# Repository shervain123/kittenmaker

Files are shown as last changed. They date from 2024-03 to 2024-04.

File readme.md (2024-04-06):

# kittenmaker

*kittenmaker* - an ESP32 based msla 3d printer

*originally created by [NyaCat42](https://github.com/NyanCat42/kittenmaker)*

# Work in progress
Parts list and instruction may be inaccurate and will be change

~As of currently I'm still waiting for all the parts to arrive~

~Parts have arrived and just notice some problems<br> fortunately it's just wrong size of magnet which I have reorder~

Wiring and pins are based off of online resources and codes

## Features 

- Web interface
- g-code parsing
- mid-print parameter updating
- magnetic, easily removable vat and printbed

## Hardware

 1. 3D printed parts in the [3D models folder](https://github.com/shervain123/kittenmaker/tree/main/3d%20models)
 2.  A Bic Crystal pen or something similar (I used a pencil)
 3. T5 lead screw and nut (the nut needs to be in a rectangle shaped instead of circular shaped)
 4. M2 & M3 screws
 5. 3w UV led 405nm wavelength
 6. A 5v fan with heat sink
 7. FEP film
 8. Bearings (683ZZ or 3x7x3mm) x6
 9. Esp32 S2 mini
 10. 2.4inch tft SPI ILI9341 display (no touch and no adapter board)
 11. Parts for driving the led (can be modified with whatever parts you have like relay)
	 -	IRFZ44N mosfet
	 -	2.2 Ohm 5W resistor
12. ~4x3mm~ 5x2mm magnets x16
13. 28byj-48-5v stepper motor with uln2003 driver
14. Micro switch
15. SD Card reader (NOT DFPlayer)

## 3D models
it is recommended to print with PETG as it is much more UV resistance than PLA but you could try and use UV protective coating on the  parts that are more likely exposed to the UV light

 ~~You will also need to print the legs.3mf and post.3mf 4 times~~ Designed a new feet / fan cover.
 
 Also for some odd reason the original does not include any way to connect the motor to the lead screw but I did find a model in older version of it which I included in the 3D models folder 

Bottom was redesigned to move the SD card and Wemos to a different location to free up some space and included screw points for the bottom feet.

## Instructions
I have decided to split them out you can find them [here](https://github.com/shervain123/kittenmaker/blob/main/instruction.md)

## Known Issue / WIP issue
Faced an issue where ESP32S2 failed to initialized and bootlooping. ~~Issue was caused by a cheap unbranded SD card that does not support SPI~~ (The SD card worked at a later date)(seems like wiring issue on the sd reader) 

Used paint primer to smooth out the resin tray, turns out primer is not resin safe. oops.

Magnet protruding from the bottom of the resin tray caused the FEP film to not seal properly and caused leaks. Might need to edit the model depending on how well your printer prints.

FEP film does NOT stick to any adhesive (tried super glue, hot glue, liquid nail(?) ), only solution that worked is sticking it with double sided tape and sealing around the tray with packing tape. 

Aluminum tape on build plate has a lot of creases, and apparently the adhesive melts in resin. Replaced with flatten soda can cut to size and superglued onto the build plate.

Z axis wobbles left to right while raising / lowering the build plate, not currently fixed and is still a work in progress. 

Benchy was printed as [Bchy](https://github.com/shervain123/kittenmaker/blob/main/images/bchy.jpg) :D

## Software

Slicer [Chitubox](https://www.chitubox.com/en/download/chitubox-free)<br>
[Chitubox v1.8.1](https://sac.chitubox.com/software/download.do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)
(Honestly I don't really like it but I don't know any better alternative so I'm stuck with this one)
<br>also if you are using newer version you will need software like uvtools to convert the ctb file to a zip. Older version can save as zip files

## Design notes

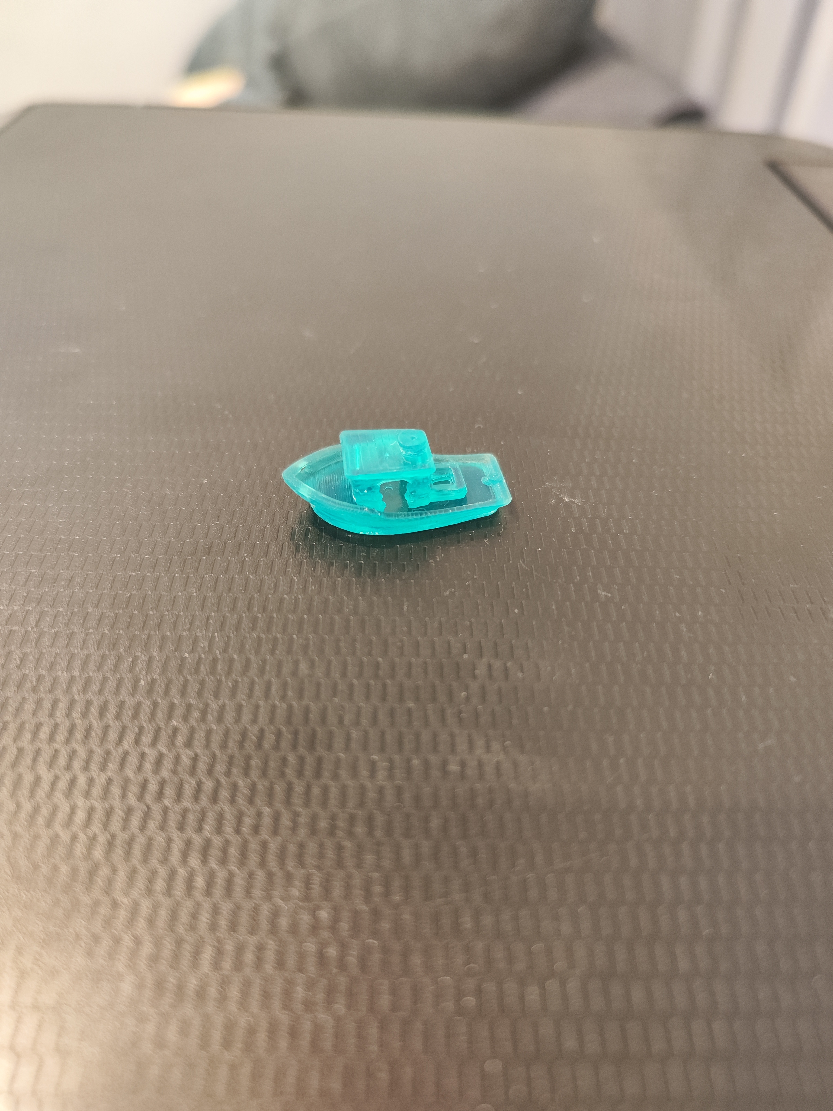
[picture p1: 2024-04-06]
images/bchy.jpg

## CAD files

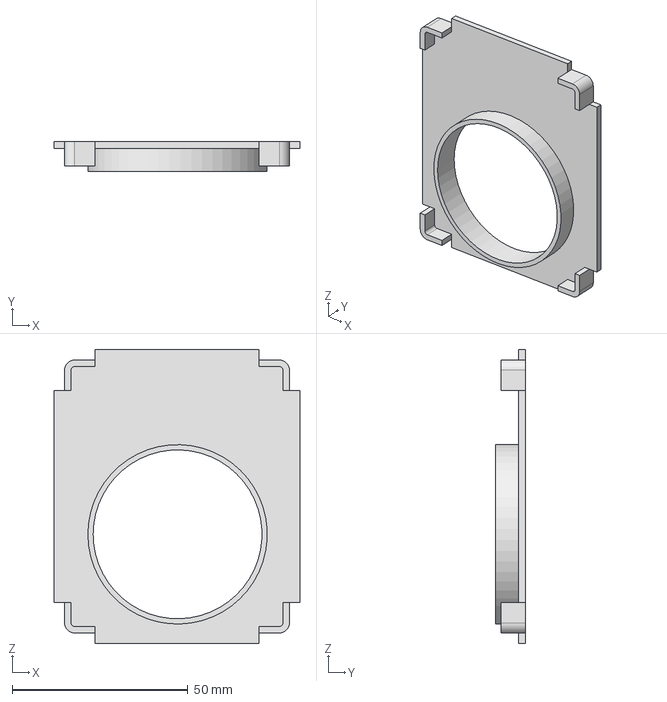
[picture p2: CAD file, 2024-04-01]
3d models/bottom cover.stp
69.9 x 8.50 x 83.6 mm

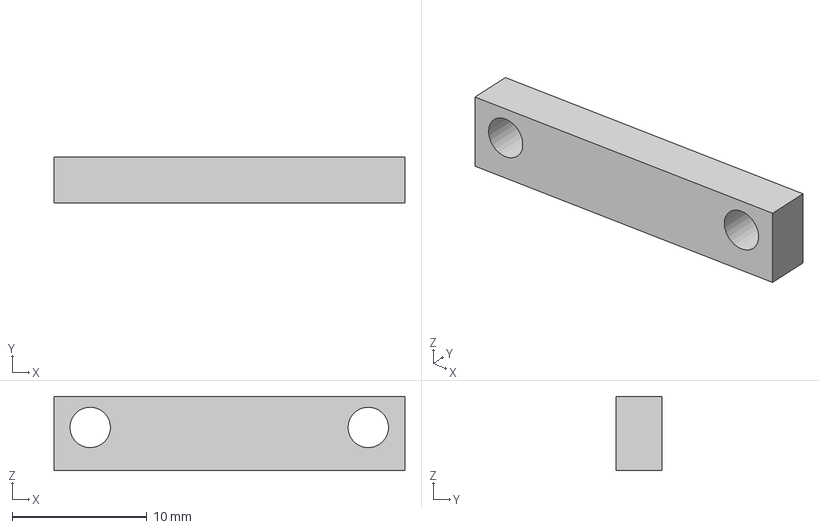
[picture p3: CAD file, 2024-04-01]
3d models/spacer.3mf
26.0 x 3.40 x 5.50 mm

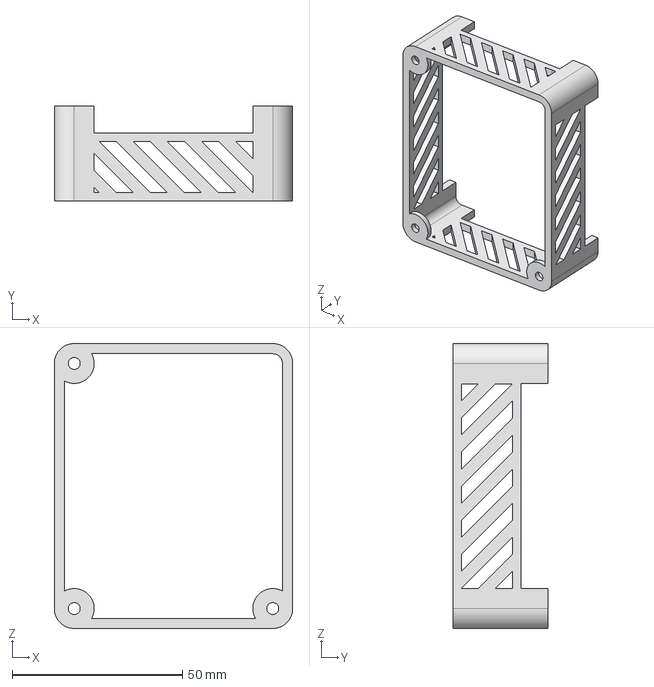
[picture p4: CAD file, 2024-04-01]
3d models/bottom.stp
69.9 x 28.0 x 83.6 mm

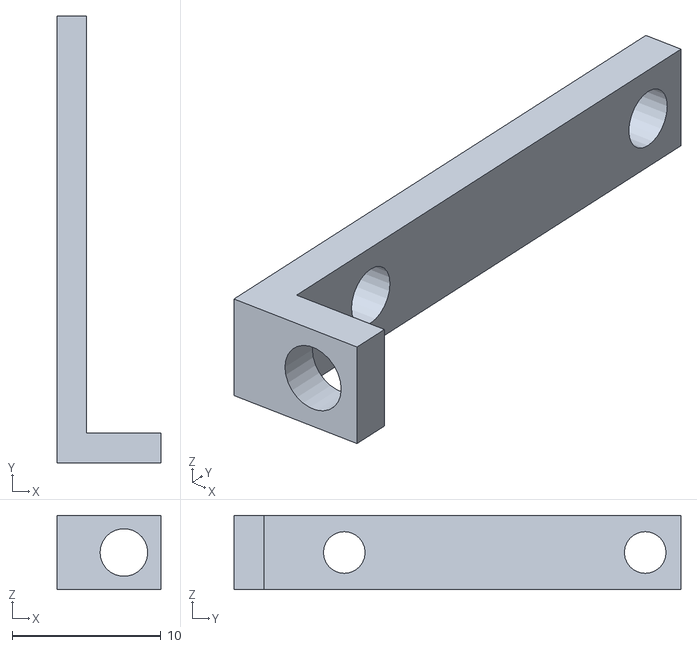
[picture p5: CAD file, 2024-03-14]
3d models/board holder.stl
7.00 x 30.0 x 5.00

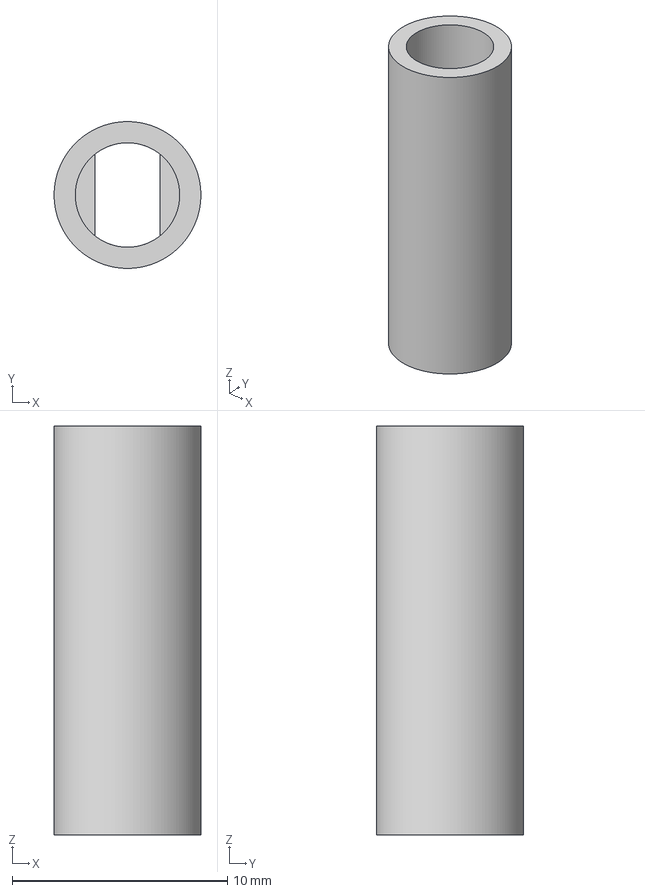
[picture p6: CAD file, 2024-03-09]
3d models/coupler.3mf
6.82 x 6.82 x 19.0 mm

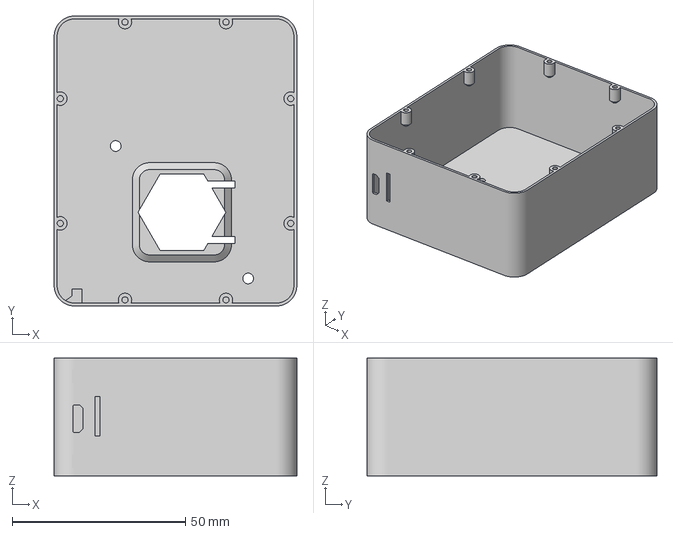
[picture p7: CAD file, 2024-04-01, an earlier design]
3d models/old/bottom (1).3mf
69.9 x 83.6 x 34.0 mm

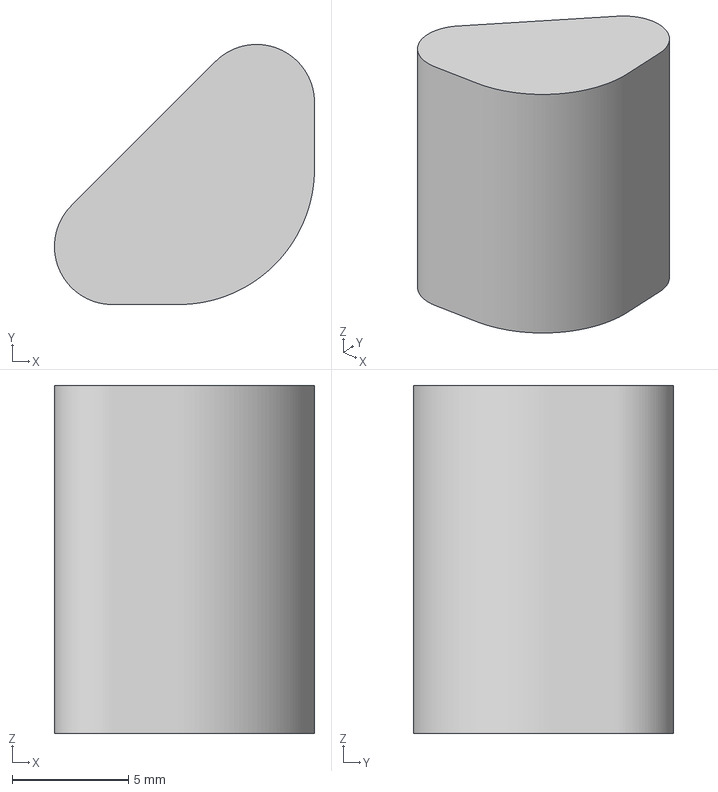
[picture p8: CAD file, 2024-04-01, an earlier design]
3d models/old/leg.3mf
11.2 x 11.2 x 15.0 mm

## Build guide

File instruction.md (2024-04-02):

[here](https://github.com)

## Wiring

### !!! WARNING ALWAYS DOUBLE CHECK WIRING BEFORE PLUGGING IN POWER AND MAKE SURE TO TEST IT BEFORE SOLDERING INTO THE BOARDS AND DISPLAY

### THE DISPLAY WIRE IS VERY CLOSE TO EACH OTHER PAY ATTENTION DURING SOLDERING AND CHECK WITH MULTIMETER THERE IS NO SHORT

The wiring is based on the code and my testing

| Item | ESP32 |
| --- | --- |
| UV LED | GPIO 37 |
| Home switch `<br>`(low trigger) | GPIO 39 |
| **Stepper motor** | |
| Pin 1 | GPIO 35 |
| Pin 2 | GPIO 33 |
| Pin 3 | GPIO 18 |
| Pin 4 | GPIO 16 |
| **SD CARD** | |
| CS | GPIO 1  |
| MOSI | GPIO 11 |
| CLK | GPIO 7  |
| MISO | GPIO 9  |
| 3v3 | 3v3 |
| **TFT DISPLAY** | |
| MISO(SDO) | GPIO 9  |
| MOSI(SDI) | GPIO 11 |
| SCLK(SCL) | GPIO 7  |
| CS(CSX) | GPIO 12 |
| DC | GPIO 5  |
| RST | GPIO3 |

If there is any problem feel free to let me know

This is the pinout for my display please check with your display first
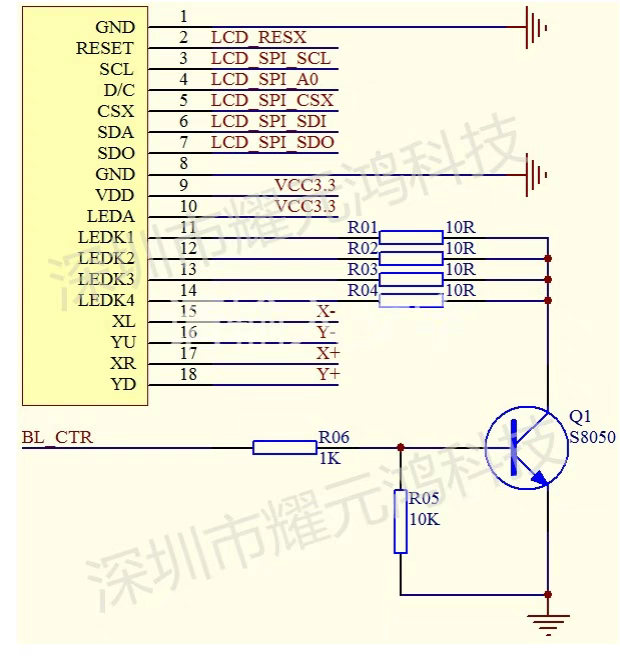
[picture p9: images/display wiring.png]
wirings


## Building instructions

This instructions is for the new bottom which I have modified from the original and with the help of tormenmashi_

If you want to follow with the original instruction, it can be found [here](https://github.com/shervain123/kittenmaker/blob/main/instruction%20old.md).

tbh this is all over the place so you should just use this as a guide for what parts goes where (I have no idea what im doing)

1. ~~Cut a piece of aluminum tape and stick it on the build plate~~ Turns out aluminum tape is trash instead, cut a aluminum can and stick it on using super glue
2. Use aluminum tape to cover the inside light tunnel to help the light disperse better
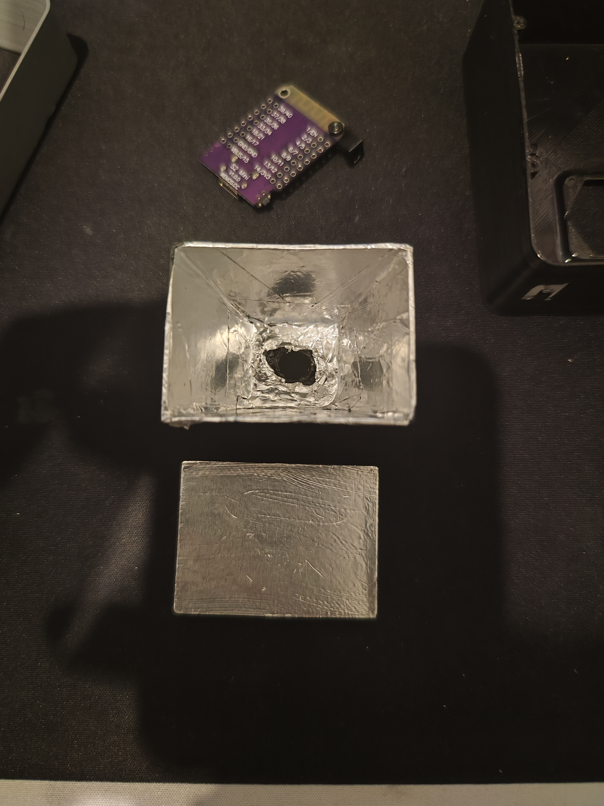
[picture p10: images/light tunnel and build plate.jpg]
Both build plate and light tunnel
   
3. Screw the bottom to the bottom case using 3 M3 screw and nuts
4. Solder wires to the sdcard board and screw it into the bottom case using 2 M2 screw and nuts
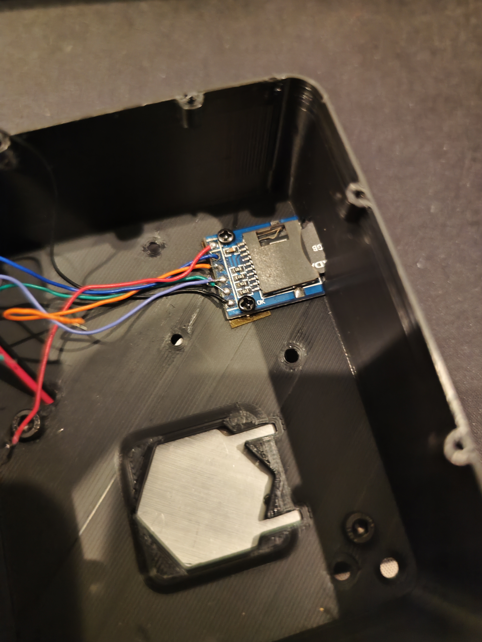
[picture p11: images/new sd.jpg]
SD screw in
   
5. Screw the wemos s2 mini with the spacer
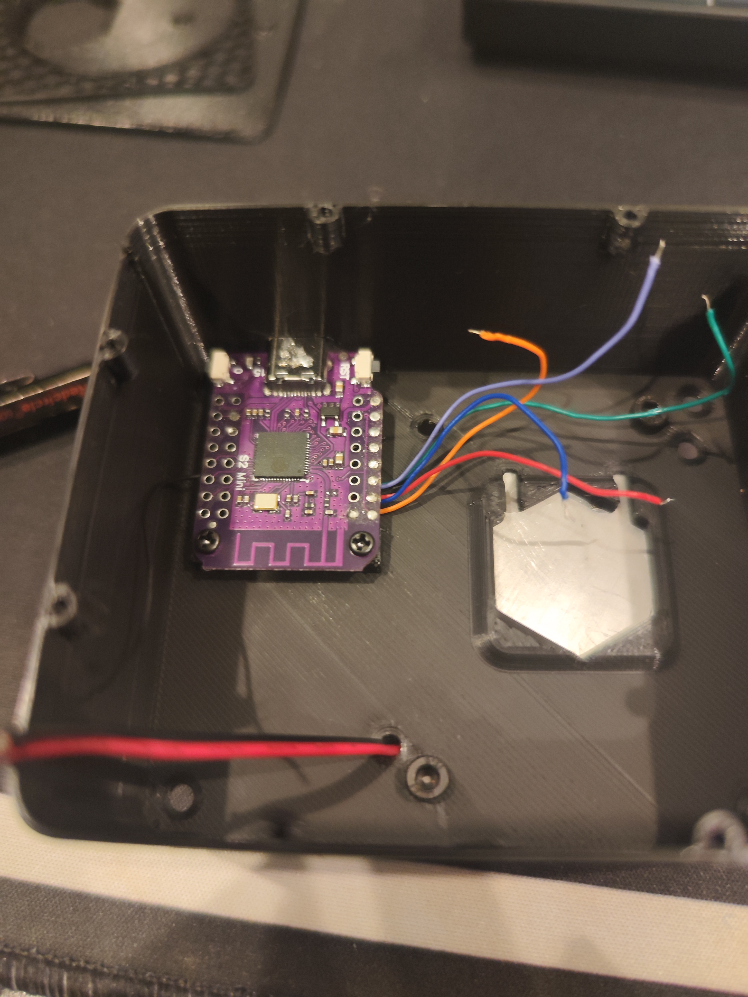
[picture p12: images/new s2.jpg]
wemos screw in
   
6. Next screw in your fan and pass the wire through the hole
7. Remove the lcd from the frame, the metal backing can be removed using a flat head screwdriver then gently bend the plastic part backwards to loosen the glue and slow the display will pop out
8. make sure you remove all the backlight component from the display and you should be left with a lcd that is see through dimly
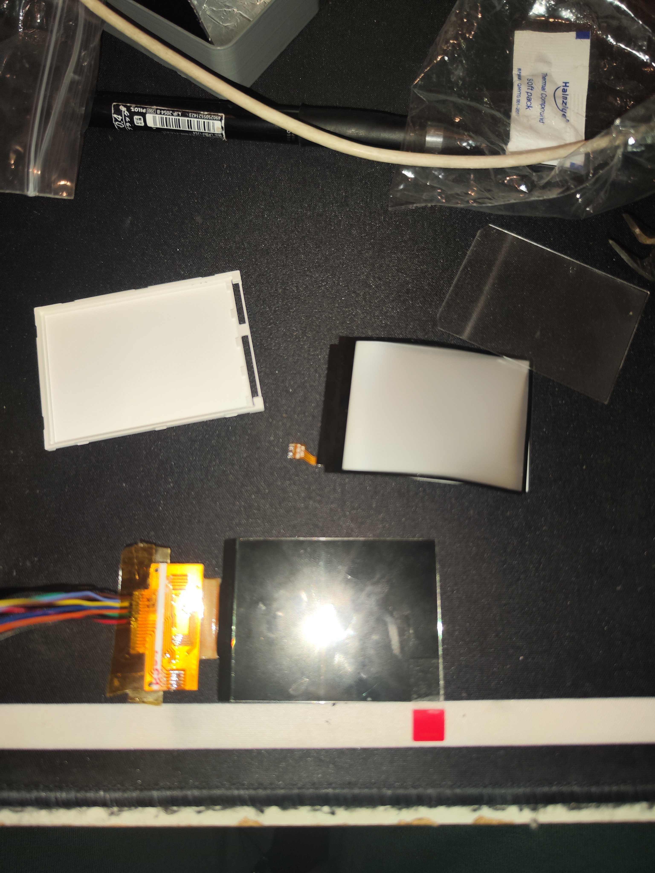
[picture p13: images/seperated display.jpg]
Naked display
   
9. pass all the wires and ribbon into the hold on the top case and place the display in it's place DO NOT FORCE IT IN IF IT DOESN'T FIT take it out and cut the edges of the top half NOT THE DISPLAY
10. Screw in the motor and the micro switch as well (use m2x10 for the switch)
11. Your finished top half should look something like this
    Top half
12. Then finished the bottom half by soldering the leds, motor controller and fan
13. Then you should solder both the lcd and sd card wires (based on the wiring diagram
14. After checking your connection plug it in  and test is everything worked
15. Screw the board to the bottom case and glue the sd card to the back
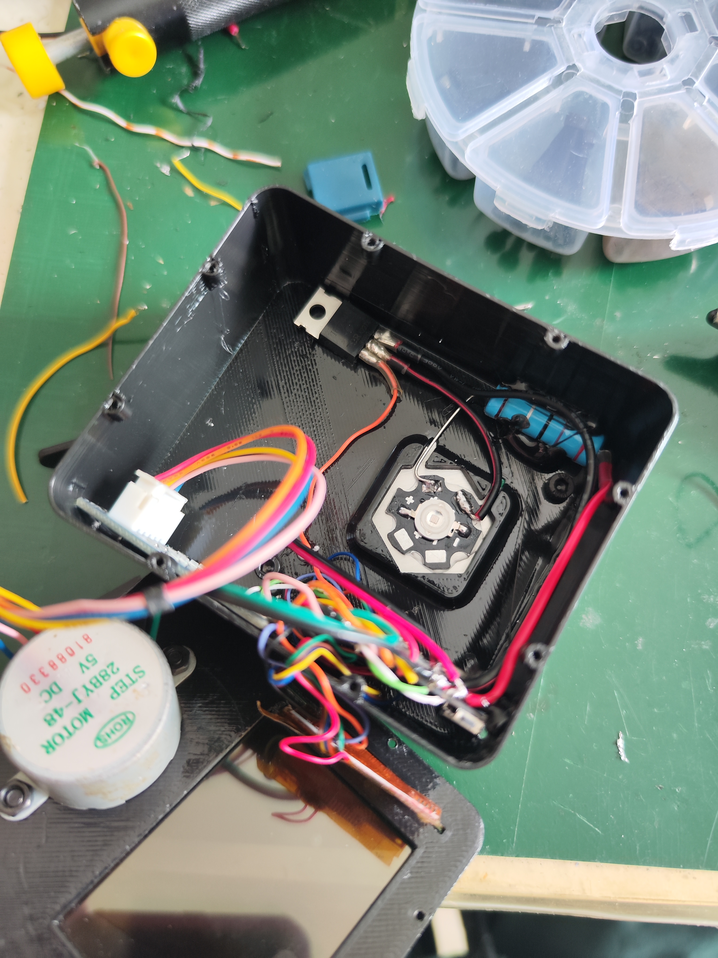
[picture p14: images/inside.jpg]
inside
    
16. Then screw in the top case with m2x4 screw
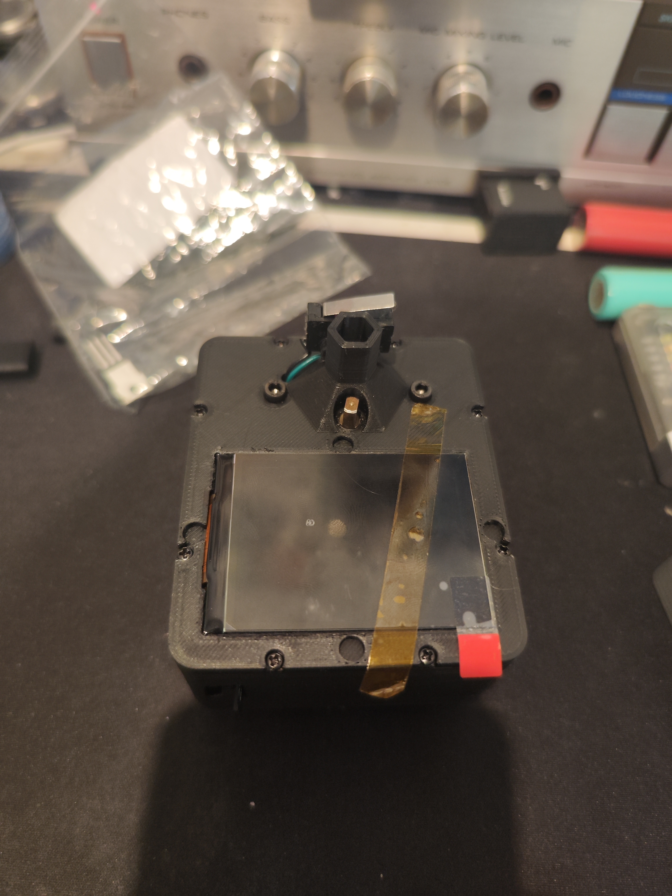
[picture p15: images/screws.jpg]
completed bottom part
    
17. Glue the feet to the bottom of the case and put coupler onto the motor
18. add glue to your bic pen and shove it in the hexagon shaped hole on the bottom and insert your lead screw into the coupler
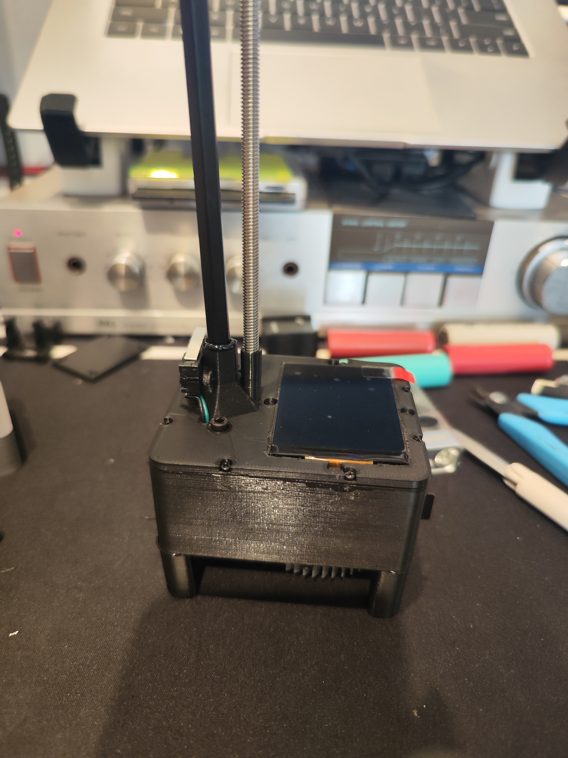
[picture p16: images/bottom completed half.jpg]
pencile
    
19. Take the top part and insert your lead screw nut you will need to drill the hole for it
    top part
20. Put the 6 bearing in place and use M3 screw to secure it in place (I run out of shorter screw)
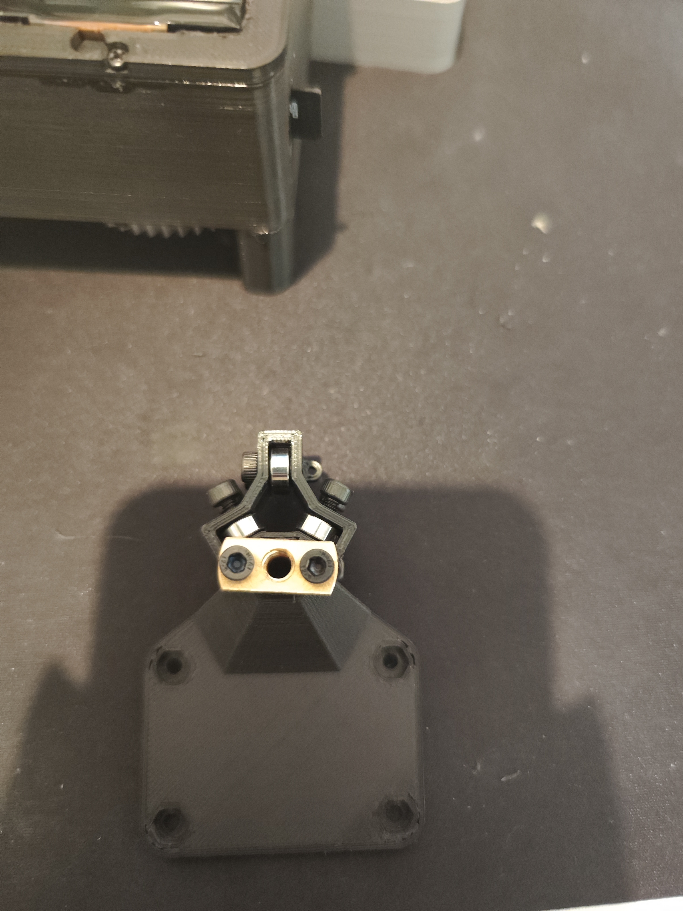
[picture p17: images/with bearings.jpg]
now with bearings!
    
21. Place 4 M3 nut in place and find the longest M3 screw you have to screw it in
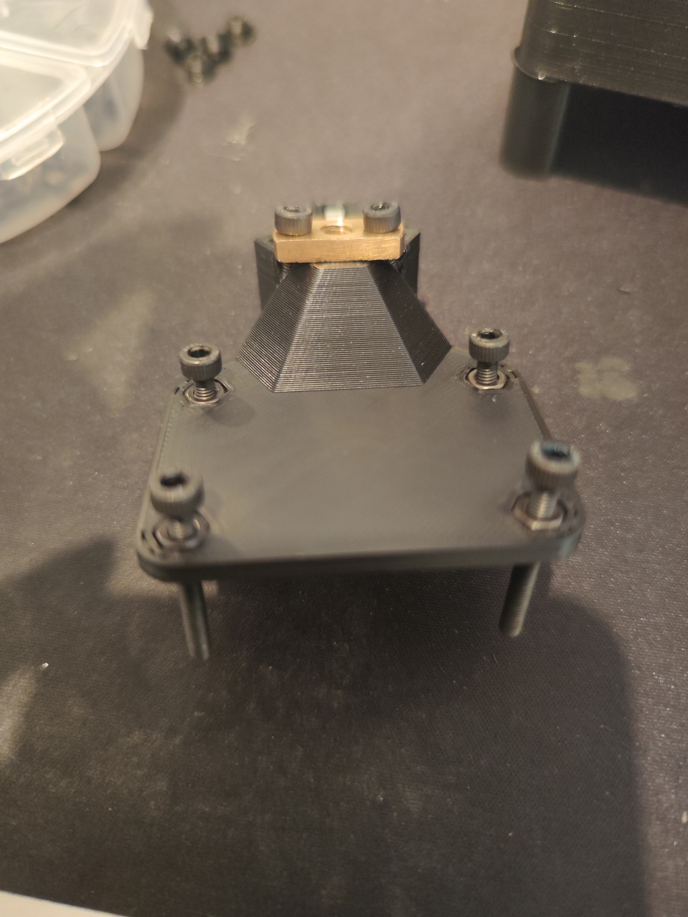
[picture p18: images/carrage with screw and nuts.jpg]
now with nuts!
    
22. Screw the plastic peg into the screw
    Pegs
23. add the longest m2 screw you have to the small part at the bearing side (this function as a home switch adjuster thingy)
24. place the magnet in all the places needs it (vat,case top, build plate and the just fron just now)
25. stick the FEP film on the vat with double side tape 
26. I have no idea how to attach the fep film superglue doesn't work
27. i think that's about it

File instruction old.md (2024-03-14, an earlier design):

## Wiring
### !!! WARNING ALWAYS DOUBLE CHECK WIRING BEFORE PLUGGING IN POWER AND MAKE SURE TO TEST IT BEFORE SOLDERING INTO THE BOARDS AND DISPLAY

### THE DISPLAY WIRE IS VERY CLOSE TO EACH OTHER PAY ATTENTION DURING SOLDERING AND CHECK WITH MULTIMETER THERE IS NO SHORT

The wiring is based on the code and my testing

|Item|ESP32  |
|--|--|
|UV LED| GPIO 37 |
|Home switch <br>(low trigger)|GPIO 39|
|**Stepper motor**||
|Pin 1|GPIO 35|
|Pin 2|GPIO 33|
|Pin 3|GPIO 18|
|Pin 4|GPIO 16|
|**SD CARD**||
|CS|GPIO 1|
|MOSI|GPIO 11|
|CLK|GPIO 7|
|MISO|GPIO 9|
|3v3| 3v3|
|**TFT DISPLAY**||
|MISO(SDO)|GPIO 9|
|MOSI(SDI)|GPIO 11|
|SCLK(SCL)|GPIO 7|
|CS(CSX)|GPIO 12|
|DC|GPIO 5|
|RST|GPIO3|

If there is any problem feel free to let me know

This is the pinout for my display please check with your display first
wirings

## Building instructions
Not yet finished building but i can add some first

tbh this is all over the place so you should just use this as a guide for what parts goes where (I have no idea what im doing)
1. Cut a piece of aluminum tape and stick it on the build plate
2. Use aluminum tape to cover the inside light tunnel to help the light disperse better
	 Both build plate and light tunnel
3. Cut out both of the tabs in front (I broke the type c port)
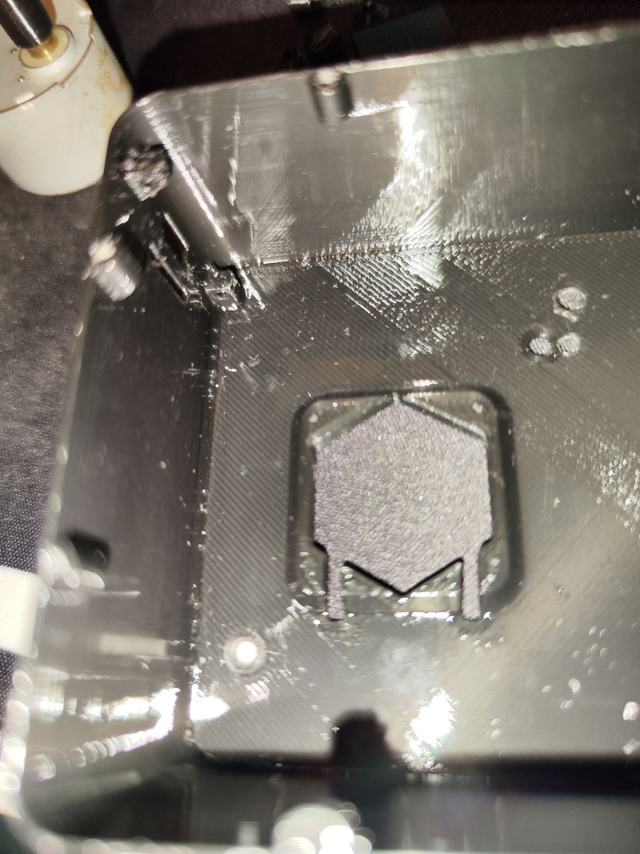
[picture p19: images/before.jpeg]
highlight of the tabs needs to be cut
	 
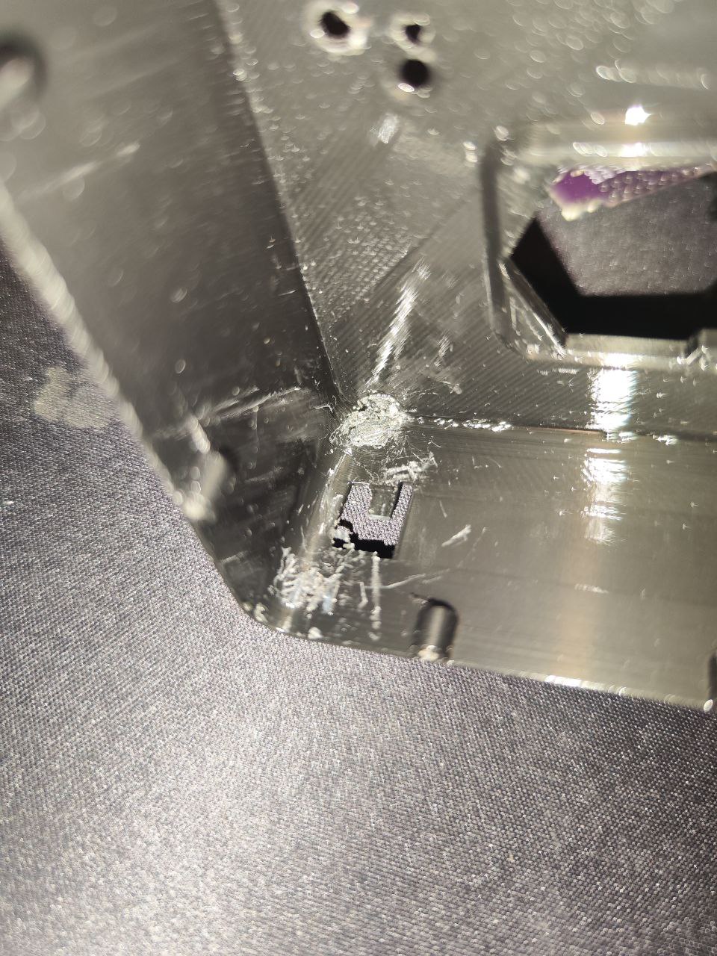
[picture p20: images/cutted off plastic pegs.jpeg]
after cutting
	 
4. Place your fan and drill a hole for wire and additional holes if necessary
5. Screw your esp32 into the holder using m2x5 and nut
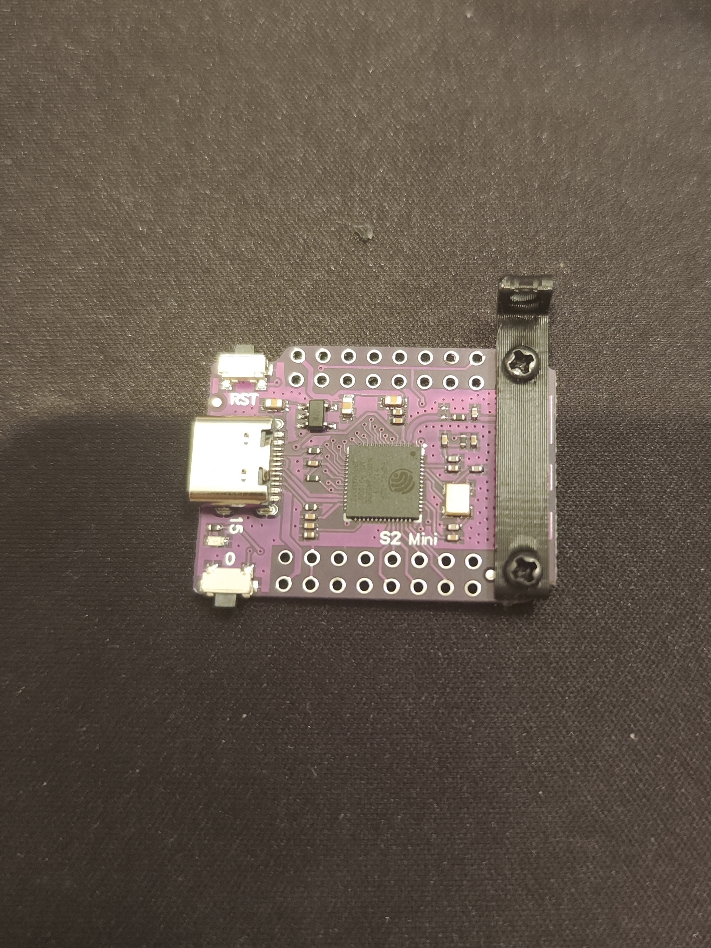
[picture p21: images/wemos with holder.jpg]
mounted wemos?
 	
7. Align in the case and mark the bottom screw hole and drill it out
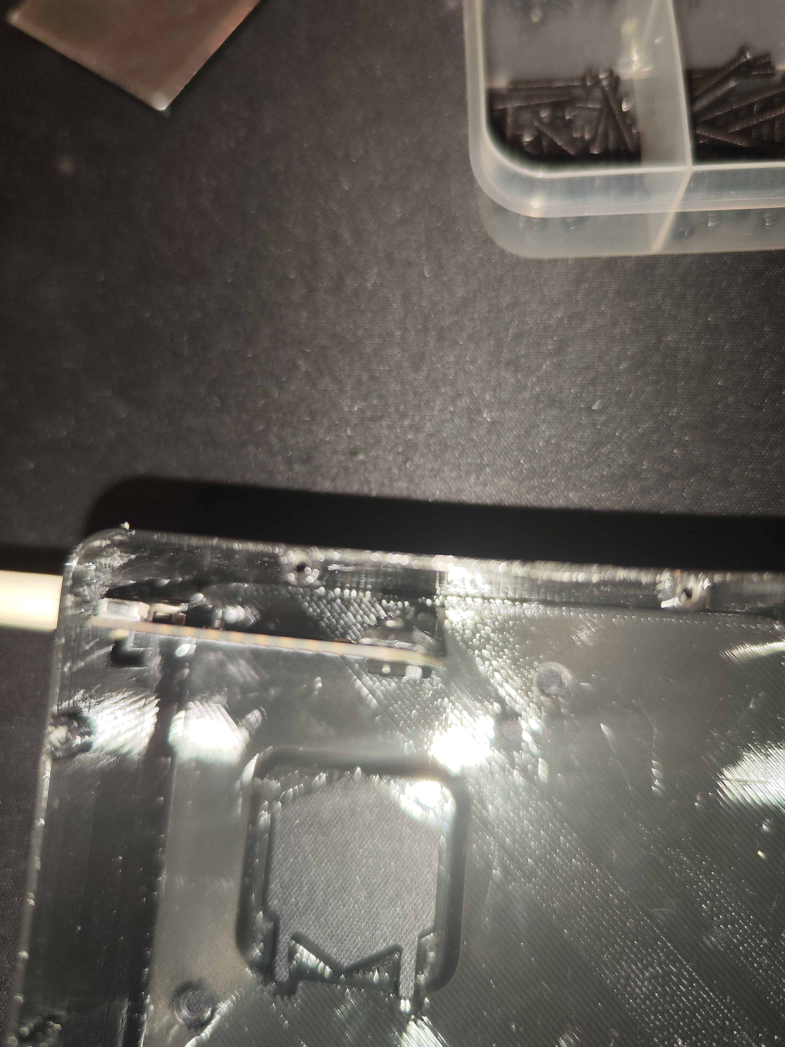
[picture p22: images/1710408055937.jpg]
image of me trying to align lol
	
8. Next screw in your fan and pass the wire through the hole
9. Remove the lcd from the frame, the metal backing can be removed using a flat head screwdriver then gently bend the plastic part backwards to loosen the glue and slow the display will pop out
10. make sure you remove all the backlight component from the display and you should be left with a lcd that is see through dimly
    Naked display
12. pass all the wires and ribbon into the hold on the top case and place the display in it's place DO NOT FORCE IT IN IF IT DOESN'T FIT take it out and cut the edges of the top half NOT THE DISPLAY  
13. Screw in the motor and the micro switch as well (use m2x10 for the switch)
14. Your finished top half should look something like this
	Top half
15. Then finished the bottom half by soldering the leds, motor controller and fan
16. Then you should solder both the lcd and sd card wires (based on the wiring diagram
17. After checking your connection plug it in  and test is everything worked
18. Screw the board to the bottom case and glue the sd card to the back
	inside 
19. Then screw in the top case with m2x4 screw
	completed bottom part
20. Glue the feet to the bottom of the case and put coupler onto the motor
21. add glue to your bic pen and shove it in the hexagon shaped hole on the bottom and insert your lead screw into the coupler
	 pencile
22. Take the top part and insert your lead screw nut you will need to drill the hole for it 
	top part 
23. Put the 6 bearing in place and use M3 screw to secure it in place (I run out of shorter screw)
	now with bearings!
24. Place 4 M3 nut in place and find the longest M3 screw you have to screw it in
	now with nuts! 
25. Screw the plastic peg into the screw
	Pegs
26. add the longest m2 screw you have to the small part at the bearing side (this function as a home switch adjuster thingy)
27. place the magnet in all the places needs it (vat,case top, build plate and the just fron just now)
28. stick the FEP film on the vat
29. i think that's about it
30. idk still waiting for my magnets

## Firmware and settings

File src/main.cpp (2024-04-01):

#include <Arduino.h>
#include <WiFi.h>
#include <AsyncTCP.h>
#include <ESPAsyncWebServer.h>
#include "SPIFFS.h"
#include <Arduino_JSON.h>


#include <SPI.h>
#include <FS.h>
#include <SD.h>
#define FS_NO_GLOBALS

#include "setup_pins.h"
#include "wifi_ssid_password.h"

#include <GCodeParser.h>
GCodeParser GCode = GCodeParser();

#include <AccelStepper.h>
AccelStepper stepper1(8, stepper_pin_1, stepper_pin_3, stepper_pin_2, stepper_pin_4); // NOTE: The sequence 1-3-2-4 is required for proper sequencing of 28BYJ-48

#include <TFT_eSPI.h>
TFT_eSPI tft = TFT_eSPI();

#define USE_LINE_BUFFER
#include "support_functions.h"

int layerheight = 0;
int exposure_time = 0;
int bottom_exposure_time = 0;
int exposure_time_print;
int stepper_speed = 1000;
int stepper_accl = 1000;
int rise_height = 0;
int steps_per_layer;
float steps_per_um = 1.0189432; // or, to be more precise - 1.018943209876543209876543209876543209876543209876543209876543209876543209876543209876543209876543209876543209876543209876543209877
int layer = 1;
bool print_started = false;
bool calibrating = false;
bool raising = false;
int rise_height_steps = 0;
bool not_home = 1;
String filename;
int bottom_layer_count = 0;
int layercount;
int bottom_rise_height = 0;
int bottom_stepper_speed = 1000;
int layerPercent = 0;
unsigned long layerTimerStart, layerTimerFinish, layerTimerElapsed;
int printTime;
String printTimeHMS = "";

AsyncWebServer server(80);
AsyncWebSocket ws("/ws");

String message = "";
String inputValue1 = String(layerheight);
String inputValue2 = String(exposure_time);
String inputValue3 = String(bottom_exposure_time);
String inputValue4 = String(rise_height);
String inputValue5 = String(bottom_rise_height);

JSONVar inputValues;
String getInputValues(){

  inputValues["inputValue1"] = String(inputValue1);
  inputValues["inputValue2"] = String(inputValue2);
  inputValues["inputValue3"] = String(inputValue3);
  inputValues["inputValue4"] = String(inputValue4);
  inputValues["inputValue5"] = String(inputValue5);
  inputValues["fileName"] = filename;
  inputValues["estimatedTime"] = printTimeHMS;
  inputValues["progressBar"] = String("width: " + String(layerPercent) + "%;");
  String jsonString = JSON.stringify(inputValues);
  return jsonString;
}

void initFS() {
  if (!SPIFFS.begin()) {
    Serial.println("An error has occurred while mounting SPIFFS");
  }
  else{
   Serial.println("SPIFFS mounted successfully");
  }
}

void initWiFi() {
  WiFi.mode(WIFI_STA);
  WiFi.begin(ssid, password);
  Serial.print("Connecting to WiFi ..");
  while (WiFi.status() != WL_CONNECTED) {
    Serial.print('.');
    delay(1000);
  }
  Serial.println(WiFi.localIP());
}

void notifyClients(String inputValues) {
  ws.textAll(inputValues);
}

void handleWebSocketMessage(void *arg, uint8_t *data, size_t len) {
  AwsFrameInfo *info = (AwsFrameInfo*)arg;
  if (info->final && info->index == 0 && info->len == len && info->opcode == WS_TEXT) {
    data[len] = 0;
    message = (char*)data;
    if (message.indexOf("1s") >= 0) {
      inputValue1 = message.substring(2);
      layerheight = inputValue1.toInt();
      notifyClients(getInputValues());
    }
    if (message.indexOf("2s") >= 0) {
      inputValue2 = message.substring(2);
      exposure_time = inputValue2.toInt();
      notifyClients(getInputValues());
    }    
    if (message.indexOf("3s") >= 0) {
      inputValue3 = message.substring(2);
      bottom_exposure_time = inputValue3.toInt();
      notifyClients(getInputValues());
    }
    if (message.indexOf("4s") >= 0) {
      inputValue4 = message.substring(2);
      rise_height = inputValue4.toInt();
      notifyClients(getInputValues());
    }
    if (message.indexOf("5s") >= 0) {
      inputValue5 = message.substring(2);
      bottom_rise_height = inputValue5.toInt();
      notifyClients(getInputValues());
    }
    if (message.indexOf("6s") >= 0) {
      print_started = true;
      notifyClients(getInputValues());
    }
    if (message.indexOf("7s") >= 0) {
      print_started = false;
      calibrating = false;
      raising = false;
      tft.fillScreen(0);
      layer = 1;
      Serial.println("stop");
      notifyClients(getInputValues());
    }
    if (message.indexOf("8s") >= 0) {
      calibrating = true;
      Serial.println("home");
      notifyClients(getInputValues());
    }
    if (message.indexOf("9s") >= 0) {
      raising = true;
      Serial.println("raise");
      notifyClients(getInputValues());
    }
    if (strcmp((char*)data, "getValues") == 0) {
      notifyClients(getInputValues());
    }
  }
}
void onEvent(AsyncWebSocket *server, AsyncWebSocketClient *client, AwsEventType type, void *arg, uint8_t *data, size_t len) {
  switch (type) {
    case WS_EVT_CONNECT:
      Serial.printf("WebSocket client #%u connected from %s\n", client->id(), client->remoteIP().toString().c_str());
      break;
    case WS_EVT_DISCONNECT:
      Serial.printf("WebSocket client #%u disconnected\n", client->id());
      break;
    case WS_EVT_DATA:
      handleWebSocketMessage(arg, data, len);
      break;
    case WS_EVT_PONG:
    case WS_EVT_ERROR:
      break;
  }
}

void initWebSocket() {
  ws.onEvent(onEvent);
  server.addHandler(&ws);
}

void secToHMS(){
  int t, h, m, s;
  t = printTime;
  
  s = t % 60;
  t = (t - s)/60;
  m = t % 60;
  t = (t - m)/60;
  h = t;

  printTimeHMS = "Estimated print time: "+String(h)+":"+String(m)+":"+String(s);

  Serial.println(printTimeHMS);
}

void parseGcode() {
      File gCodeFile = SD.open("/run.gcode");
    if (gCodeFile)
    {
      int settingsLenght = 1;
      while (gCodeFile.available() && settingsLenght <= 27)
      {
        if (GCode.AddCharToLine(gCodeFile.read()))
        {
          GCode.ParseLine();
          GCode.RemoveCommentSeparators();
          if(settingsLenght == 8){
              layerheight = String(GCode.comments).substring(12).toFloat()*1000;
              Serial.println(layerheight);
          }if(settingsLenght == 15){
              exposure_time = String(GCode.comments).substring(19).toInt();
              Serial.println(exposure_time);
          }if(settingsLenght == 17){
              bottom_exposure_time = String(GCode.comments).substring(24).toInt();
              Serial.println(bottom_exposure_time);
          }if(settingsLenght == 19){
              rise_height = String(GCode.comments).substring(22).toInt();
              Serial.println(rise_height);
          }if(settingsLenght == 21){
              stepper_speed = String(GCode.comments).substring(21).toInt();
              Serial.println(stepper_speed);
          }if(settingsLenght == 1){
              filename = String(GCode.comments).substring(9);
              Serial.println(filename);
          }if(settingsLenght == 23){
              bottom_layer_count = String(GCode.comments).substring(17).toInt();
              Serial.println(bottom_layer_count);
          }if(settingsLenght == 25){
              layercount = String(GCode.comments).substring(11).toInt();
              Serial.println(layercount);
          }if(settingsLenght == 26){
              bottom_rise_height = String(GCode.comments).substring(22).toInt();
              Serial.println(bottom_rise_height);
          }if(settingsLenght == 27){
              bottom_stepper_speed = String(GCode.comments).substring(21).toInt();
              Serial.println(bottom_stepper_speed);
          }settingsLenght++;
        }
      }  
    }
  inputValue1 = String(layerheight);
  inputValue2 = String(exposure_time);
  inputValue3 = String(bottom_exposure_time);
  inputValue4 = String(rise_height);
  inputValue5 = String(bottom_rise_height);
  printTime = bottom_layer_count*bottom_rise_height*2+(layercount-bottom_layer_count)*rise_height*2+bottom_layer_count*bottom_exposure_time+(layercount-bottom_layer_count)*exposure_time;
  Serial.println(printTime);
  secToHMS();
}


void setup() {

  pinMode(Home_Switch, INPUT_PULLUP); // homing switch
  pinMode(UV_LED, OUTPUT);       // uv led driver (high is off)
  digitalWrite(UV_LED, 0);       // turn led off

  Serial.begin(115200);

  if (!SD.begin(1)) {
    Serial.println(F("SD.begin failed!"));
  }

  tft.begin();
  tft.setRotation(1);

  parseGcode();

  initFS();
  initWiFi();
  initWebSocket();
  
  server.on("/", HTTP_GET, [](AsyncWebServerRequest *request){
    request->send(SPIFFS, "/index.html", "text/html");
  });

  server.on("/preview", HTTP_GET, [](AsyncWebServerRequest *request){
    request->send(SD, "/preview.png", "image/png");
  });
  
  server.serveStatic("/", SPIFFS, "/");

  server.begin();
}

void loop() {

  stepper1.setAcceleration(stepper_accl);
  stepper1.setSpeed(stepper_speed);
  stepper1.setMaxSpeed(stepper_speed);
   
  not_home = digitalRead(Home_Switch);

  if(raising == true){
    Serial.println("raisung");
    stepper1.moveTo(stepper1.currentPosition() + steps_per_um * 20000);
    do {
     stepper1.run();
    } while (stepper1.distanceToGo() != 0 && raising == true);
    raising = false;
  }

  if(calibrating == true){
    Serial.println("calibrating");
    stepper1.moveTo(stepper1.currentPosition() - steps_per_um * 100000);
    do {
     stepper1.run();
     not_home = digitalRead(Home_Switch);
    } while (not_home == 1 && stepper1.distanceToGo() != 0 && calibrating == true);
      not_home = digitalRead(Home_Switch);
    if(not_home == 0){
      calibrating = false;
      stepper1.moveTo(0);
      stepper1.setCurrentPosition(0);
    }
  }

  if(print_started == true){

    Serial.println(printTimeHMS);

    String layerstr = String(layer);
    String layerfilename = "/"+layerstr+".png";
    const char* layerfilenameconst = layerfilename.c_str();
    setPngPosition(0, 0);
    load_file(SD, layerfilenameconst);

    if(layer <= bottom_layer_count){
      exposure_time_print = bottom_exposure_time;
    }else {
      exposure_time_print = exposure_time;
    }

    digitalWrite(UV_LED, 1);
    delay(exposure_time_print*1000);
    digitalWrite(UV_LED, 0);

    steps_per_layer = steps_per_um * layerheight + 0.5;
    if(layer <= bottom_layer_count){
      rise_height_steps = bottom_rise_height * 1000 * steps_per_um;
      stepper1.setSpeed(bottom_stepper_speed);
      stepper1.setMaxSpeed(bottom_stepper_speed);
    }else {
      rise_height_steps = rise_height * 1000 * steps_per_um;
      stepper1.setSpeed(stepper_speed);
      stepper1.setMaxSpeed(stepper_speed);
    }


    layerTimerStart=millis();

    stepper1.moveTo(stepper1.currentPosition() + steps_per_layer + rise_height_steps);

    do {
      stepper1.run();
    } while (stepper1.distanceToGo() != 0);

    stepper1.moveTo(stepper1.currentPosition()-rise_height_steps);

    do {
      stepper1.run();
    } while (stepper1.distanceToGo() != 0);

    layerTimerFinish=millis();
    layerTimerElapsed=layerTimerFinish-layerTimerStart;
    Serial.println(layerTimerElapsed);

    if(layer <= bottom_layer_count){
      printTime = (bottom_layer_count-layer)*layerTimerElapsed/1000+(layercount-bottom_layer_count)*rise_height*(layerTimerElapsed/1000/bottom_rise_height)+(bottom_layer_count-layer)*bottom_exposure_time+(layercount-bottom_layer_count)*exposure_time;
    }else {
      printTime = (layercount-layer)*layerTimerElapsed/1000+(layercount-layer)*exposure_time;
    }
    Serial.println(printTime);
    secToHMS();

    layer = layer + 1;
    layerPercent = layer*100/layercount;
      
    if (layercount < layer) {
      print_started = false;
      tft.fillScreen(0);
      layer = 1;
      raising = true;
    }
     
  }

  ws.cleanupClients();
}

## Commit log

2024-03-09 Added coupler from old version of the repository
    [coupler.3mf]
2024-03-12 Update readme.md
    pin changes
2024-04-01 New bottom design
    [board holder.stl, bottom (1).3mf, bottom cover.stp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]
2024-04-01 inverted logic for uv led
    [main.cpp]
